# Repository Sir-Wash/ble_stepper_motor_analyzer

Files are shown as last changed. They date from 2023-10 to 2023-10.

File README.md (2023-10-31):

# BLE STEPPER MOTOR ANALYZER

> **_NOTE:_** As for June 24th 2023, added under the spec table a discussion regarding the **max stepper voltage** that can be used.

------
<p align="center">
  <br>
  The analyzer device of the reference design here<br>
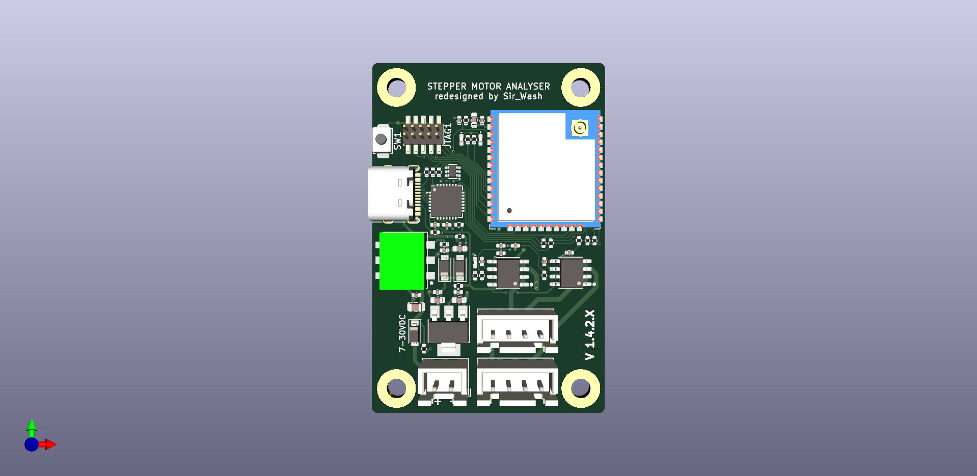
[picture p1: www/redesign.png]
  
</p>

My redsigned design can be found in "\ble_stepper_motor_analyzer\kicad\JLCPCB\Sir_Wash_Redesign"

<p align="center">
  The analyzer's app<br>
  
</p>

**A short video** of the app is available here https://vimeo.com/798169140

---
- [BLE STEPPER MOTOR ANALYZER](#ble-stepper-motor-analyzer)
  - [Description](#description)
  - [Design Highlights](#design-highlights)
  - [How does it work?](#how-does-it-work)
  - [Specification](#specification)
  - [Installing the device in your 3D printer](#installing-the-device-in-your-3d-printer)
  - [Using the Analyzer app.](#using-the-analyzer-app)
    - [Running the Analyzer app using a provided binary](#running-the-analyzer-app-using-a-provided-binary)
    - [Running the Analyzer app using the Python source files](#running-the-analyzer-app-using-the-python-source-files)
    - [Understanding the Analyzer app screen](#understanding-the-analyzer-app-screen)
    - [The Analyzer app buttons](#the-analyzer-app-buttons)
    - [Analyzer app command line flags](#analyzer-app-command-line-flags)
  - [Updating the firmware](#updating-the-firmware)
  - [Building your own device](#building-your-own-device)
  - [Antenna selection](#antenna-selection)
  - [Connectors](#connectors)
  - [3D Models](#3d-models)
  - [Troubleshooting connection issues](#troubleshooting-connection-issues)
  - [Hardware design files](#hardware-design-files)
  - [Firmware development](#firmware-development)
  - [Analyzer App Python development](#analyzer-app-python-development)
  - [FAQ](#faq)

---

## Description

The BLE Stepper Motor Analyzer ('the analyzer') is a low-cost, open source system that analyzes stepper motor signals and display the the data in real time on a computer screen. The system includes two parts:

1. **The Stepper Motor Probe** ('the device'). This is a small electronic board that monitors the currents through the stepper motor wires, extracts information such as steps, and speed, and transmits the data via Bluetooth BLE.

2. **The Analyzer App** ('the app'). This is a Python program that runs on a Windows, MaC OSX, or Linux PC, and displays the stepper information in real time in a graphical view.

The following block diagram shows how the device and the app related to the controller and stepper motor of an existing system such as a 3D printer. 

<p align="center">
 System Block diagram<br>
  
</p>

## Design Highlights
* The device is passive and does not interfere with the operation of the stepper motor, regardless if it is in use or turned off. Furthermore, the stepper signals are galvanically isolated from the electronics.
* Embedding the device in a 3D printer is simple. It has a small footprint, operates on 7-30 VDC, and can use a small external sticker antenna that overcomes shielding by the printer enclosure.
* The design is in the public domain (Creative Commons CC0) and can be used also commercially. Attribution and code sharing are not required.
* The device design is low cost and can be ordered fully assembled from JLCPCB or similar services.
* The device firmware can upgraded by users using a standard USB cable, no tools or adapter required.
* Each device has its fixed unique address such that multiple devices can be used and addressed independently (e.g. one for each stepper motor in your printer).
* Open BLE and Python APIs supports custom monitoring apps, such as specialized analyzers or mobile apps.

## How does it work?
The device contains two galvanic isolated current sensors that sense the currents through the two stepper coils. These values are measured 40,000 times a second and firmware on the device analyzes them and extracts information such as step count, speed, and current patterns. A Bluetooth BLE radio then transmits the data to the app which displays it in a graphical form.

 <p align="center">
 Device Block diagram<br>
  
</p>

## Specification

| Item | Specification |
| :--- | :--- |
| Supply voltage | 7-30 VDC |
| Stepper motor voltage | See note below |
| Power consumption | 1W max |
| Firmware update connector | USB Type C. |
| SOIC Module | ESP32-WROOM-32U-N4. |
| Current measurement | +/-2.5A per coil. |
| PCB | 39mm x 43mm, two layers. |
| Antenna | 2.4Ghz external antenna IPX IPEX connector. |
| Simultaneous connections | 1 max. |
| Protocol | BLE 4.1 or higher, with Data Length Extension feature. |
| Current sensors | CC6920BSO-5A |
| Zero calibration | Using onboard button. |
| Count direction | User selected (doesn't change motor direction). |
| Sampling rate | 40Khz per channel. |
| Sampling resolution | 12bits. |
| Current accuracy | estimated at +/- 2%. |
| Max step rate | 5K full steps/sec. |
| Step resolution | 1/100th of a full step. |
| Firmware programming language | C++ |
| Firmware programming IDE | VSCode, Platformio, ESPIDF framework. |
| Firmware debugging | Via optional 10 pins JTAG connector. |
| Electronic design tool | Kicad. |
| Mechanical design tool | Onshape. |
| Open source license | Creative Commons CC0. |

> **_NOTE:_**  The analyzer uses current sensors CC6920BSO-5A current
sensors which provides galvanic isolation between the stepper motor wires and the circuitry and input voltage of the analyzer. As a result, the stepper motor voltage is not limited, and is independent, of the supply voltage. While the sensors are specified as 3500V RMS isolation, the PCB was definitely not designed for that voltage in mind and use only 6mil clearance between the traces. Some information on the internet such as https://www.smpspowersupply.com/ipc2221pcbclearance.html suggests that this qualifies it to 50 or even 100v, but since we are not safety experts, we tested it with only 24V steppers.

## Installing the device in your 3D printer

1. Print a device carrier using a 3D printer (STL model included here) and attach the device to the carrier using two pieces of 3M VHB 1mm sticky tape or similar.
2. Attach the device carrier to the 3D printer using an additional piece of 3M VHB tape.
3. Connect the external antenna and attach the antenna to the outside of the printer.
4. Connect the motor driver and stepper motor to the two connectors as shown in the wiring diagram below. The two connectors form a path through path, such that one pair of adjacent pins are used for one coil and the other pair for the second coil.
5. Connect 7-30VDC power to the VIN connector of the device. Pay attention to polarity, though the device will not get damaged by reverse polarity. 
6. Do not connect anything to the USB connector. This connector is intended for firmware flashing only.
7. The device installation is complete. You can use your 3D printer just as you did before, regardless if the analyzer app is active or not. To monitor the stepper while your printer is turned on, use the provided analyzer app on your Windows, Mac, or Linux PC as described below. 

&nbsp;

<p align="center">
  Wiring Diagram<br>
  
</p>

## Using the Analyzer app.

### Running the Analyzer app using a provided binary
The simplest way to run the analyzer app on your computer is to look for an  executable file for your system under the 'release' directory in this repository. They also released as 'release.zip' file.

> **_NOTE:_**  The single binary files are created from the app's Python code using the Pyinstaller tool and the scripts in the python/pyinstaller directory.

### Running the Analyzer app using the Python source files
If a single app binary is not available for your system, or if you prefer to run the Python code directly, you will first need to do a few preparation to satisfy the prerequisites of the Python code.

1. Install Python on your computer. Prefer the latest stable version.
2. Clone the repository on your computer or download and extract the 'python.zip' release file.
3. Install the required python modules by running this command the 'python' directory :
   
```
pip install -r requirements.txt
```
4. Make sure that your analyzer device is powered on and start the app using the command

```
python analyzer.py
```

> **_NOTE:_**  When the device is idle, its LED blink at a rate of about 1 blink per second. When connected to the app, it blink faster about 3 blinks per second. The app can connect to a device only when it's idle as indicated by the slower blink rate.

### Understanding the Analyzer app screen

<p align="center">
  
</p>

The apps screen contains the following graphs

* [A]. A rolling chart with distance in steps. Updated 50 times a second.
* [B]. A rolling chart with speed in steps/sec. Updated 50 times a second.
* [C]. A rolling chart with stepper absolute current in Amps. Updated 50 times a second. The absolute current of a stepper is sqrt(A^2 + B^2) where A and B are the momentary currents of coils A, B respectively.
* [D] A histogram of current vs speed that shows how well the driver is able to maintain the stepper current at various speeds. High coil inductance of low power voltage result in significant current level at higher speeds.
* [E] A histogram that shows the relative time spent in each speed range.
* [F] A histogram that shows the relative distance done in each speed range.
* [G] A phase (Lissajous curve) graph that shows the 'cleanliness' of the sine/cosine current signals the driver sends to the motor.
* [H] An oscilloscope graph that shows current samples from the two coils. During stepper movement in a constant speed, they should look like sine/cosine waves. 

> **_NOTE:_**  In the oscilloscope graph, a single sine or cosine cycle represents 4 stepper full steps, as shown in the graph below.

<p align="center">
  
</p>

### The Analyzer app buttons
The Analyzer app contain the button listed below. 

> **_NOTE:_**  The buttons affect the app only and do not interfere with the operation of the motor.

* **Toggle Dir** - Click to change the direction of step counting.
* **Reset Data** - Click to clear the histograms and step count.
* **Time Scale X** - Click to toggle the sampling time of the signals shown in the phase graph [G] and oscilloscope graph [H] to match the movement speed. As a rule of thumb, you want to have at least one full sine/cosine wave, with higher values for slower stepper movements.
* **Pause** - Click to pause/resume the display. Useful examine interesting captured data.

> **_NOTE:_** The graphs are implemented using pyqtgraph and thus provide additional functionality that is accessible by a right mouse click on the graphs.

### Analyzer app command line flags

**--help** Prints a list with the available flags.

**--scan** The analyzer will scan for BLE devices for a few seconds, print a list of  devices it found and exit. This intended for diagnostics. The stepper motor analyzer devices have names that look like <si>STP-0C8B95F2B436</i>.

```
python analyzer.py --scan
```

**--device** Instructs the analyzer to not search on start for available devices, and instead, connect to the device with given name directly. If you set in the device a nick name using the --set-nickname flag below, you can also use that nickname as a value of the --device falg. 

```
python analyzer.py --device "STP-0C8B95F2B436"

python analyzer.py --device "X-AXIS"
```

**--set_nickname** Running the analyzer with this flags sets on the device a user friendly nickname that can be used as an alternative value for the *--device* flag. That nickname is also shown in the title of the Analyzer graphical view.

```
python analyzer.py --set_nickname "X-Axis"
```

**--max-amps** If you monitor a low current stepper motor such as a 600ma extruder motor, you can use this flag to limit the range of the current display in the Phase and Oscilloscope graphs, to zoom in on details.
```
python analyzer.py --max-amps 0.8
```

***--units*** The default units for stepper distance or rotation are full steps. You can use this flag to display other units such as mm, degrees, or extrusion mm^3. 
```
python analyzer.py --units "mm"

python analyzer.py --units "degrees"

python analyzer.py --units "mm^3"
```

**--steps_per_unit** If you are using the **--units** flag, use this flag to specify the number of full motor steps that correspond to one unit. For example, if your extruder esteps value is 540 micro steps per mm, with 16 microsteps per full step, specify the flags below:
```
python analyzer.py --units=mm --steps_per_unit 33.75
```

## Updating the firmware

To flash a firmware version follow these steps.

1. Download the release.zip file of the desired release and extract it.
2. Disconnect the power connector of the device and connect it to your computer using a USB cable.
3. Run the flash script for your Windows, Mac or Linux computer. For example:
```
flash.bat
```
 4. Verify that the the script completed with no errors and that the LED on the device is blinking at about one blink per second. The device with the new firmware is ready.

## Building your own device

1. Order assembled boards (recommended), or just order bare PCBs and assemble the components yourself. Production files for JLCPCB PCB, including for the SMT service are included in this repository.
2. Connect the device to a computer via a USB cable and notice that one LED turn on solid to indicate 3.3V power.
3. Flash the device with firmware as explained above.
4. Calibrate the current sensors for zero level by long pressing the switch until the second LED will blink 3 times to indicate that the calibration values were saved in the non volatile memory.
5. Connect an antenna, run an analyzer program as explain above and that you see some signals from the device. The LED on the device will blink faster to indicate an active connection.
6. The device is now ready for installation in the 3D printer or for shipping to your customers.

* **Schematic**: https://github.com/zapta/ble_stepper_motor_analyzer/blob/main/kicad/stepper_monitor.pdf
* **JLCPCB production files**: https://github.com/zapta/ble_stepper_motor_analyzer/tree/main/kicad/JLCPCB

> **_NOTE:_**  Resistor R16 acts as a jumper and allows to disconnect the 3.3V supply from the rest of the electronics. This is useful when diagnosing power issues.

## Antenna selection

The external antenna should  satisfy these requirements:
* Specified for the Bluetooth band of 2.4GHZ.
* Having a connector that match the ESP32 WROOM module. The connector has several names including IPEX, U.FL, or MHF1, but it's easier to distinguish it by its wider body.

<p align="center">
  
</p>

<p align="center">
  Inexpensive Aliexpress sticker antennas.<br>
  
</p>

## Connectors

* **Stepper Motor Connectors** - KF2510 connector 2.54mm pitch, female, 4 wires.
* **Vin connector** - Dupont 2.54mm pitch, female, 2 wires. 

## 3D Models

3D Models of the carrier and a cover for shipping are available at https://github.com/zapta/ble_stepper_motor_analyzer/tree/main/3D

<p align="center">
  
</p>

## Troubleshooting connection issues

The analyzer requires on the PC side support for Bluetooth BLE 4.1 or higher with support for the Data Length Extension feature. It is expected that most computer come with a built in adapters that support
this standard, but we also observed a very low cost BeeLink mini computer that came with an old internal Bluetooth adapter that doesn't support this standard.

The workaround in this case is to **disable the internal Bluetooth adapter** and use an **external USB Bluetooth adapter** that has an external antenna for better range. For example we had good result with this adapter that as of 2023 cost about $15 https://www.amazon.com/gp/product/B09KGVFX1K, which is based on the RTL876B chip.

<p align="center">
  
</p>

> **_NOTE:_**  Installing a RTL876B based adapter on Ubuntu requires a minor tweak of the firmware file names as explained at https://fosspost.org/fix-bluetooth-rtl8761b-problem-on-linux-ubuntu-22-04/. Also, 

The symptoms of a PC bluetooth adapter that doesn't support the required protocol are that the device shows up when running *analyzer --scan* but when running the analyzer without the *--scan* flag, it fails to connect to the device.  For the more technical readers, a discussion on this topic is available here https://github.com/hbldh/bleak/issues/1227#issuecomment-1435708347

## Hardware design files

The Kicad source files and the generated JLCPCB production files are available under the *kicad* directory of this repository. As of Mar 2023, we are using Kicad 7.0, and the built in plugins **Fabrication Toolkit** and **Interactive Html Bom**.

## Firmware development

This list below outlines the steps to set up your own firmware development environment.

1. Install Visual Studio Code (VSC).
2. In Visual Studio Code, enable the <i>platformio</i> extension.
3. Download or clone this git repository on your computer.
4. In VSC, select <i>File | Open Folder</i> and select the 'platformio' directory.
5. Connect a device to your computer using a USB cable. This will create a serial port on your computer.
6. Click on the platformio <i>Upload</i> icon at the bottom of the screen (right arrow icon) and platformio will automatically install all the dependencies, build the project, and upload it to your device via the serial port.  
7. For more information on how to use platformio, check http://platformio.org.

> **_NOTE:_**  For optional hardware debugging (breakpoints, single step, etc), you will need an Espressif ESP-Prog Development Board, and to solder on your device a 10 pins JTAG connector.

> **_NOTE:_** It's OK to connect a stepper motor to the device while you develope code since the stepper signals are galvanically isolated from the USB interface and from your computer.

> **_NOTE:_** It is recommended to not connect VIN and the USB connectors at the same time to avoid ground loop, in case both the Vin power supply and your computer are grounded independently.

## Analyzer App Python development

The Analyzer's Python app is stored in the 'python/analyzer' directory and uses a library at python/common. The app is based on Bleak (BLE client) PyQtGraph (a graphing library) and uses asyncio for non blocking background operation. The list of requires python modules is in requirements.txt and they can be installed using the command

```
pip install -r requirements.txt
```

## FAQ

**Q**: This is an exciting project, can I help?

A: Of course, contribution of code, documentation, test programs or ideas are welcome.

---

**Q**: I want to monitor multiple motors in my 3D printer. Is it possible?

**A**: Of course. Simply install a device for each stepper motor you want to monitor. 

---

**Q**: I am using multiple devices, how can I select which one I connect to? 

**A**: Each device has a fixed unique name such STP-0C8B95F2B436. When you run the analyzer app, it will allow you to select a device, if more than one are available, or you can use the --device flag to force a specific device.

---

**Q**: How far can my computer be away from my 3D printer? 

**A**: Bluetooth BLE radio communication is intended for short distances of a few yards. If the radio link will not be reliable, the analyzer program will detect data gaps and will report it in its console log.

---

**Q**: This system can be a great idea for a Crowd Compute campaign. Can I do that? 

**A**: Of course. The design is in public domain and commercial usages are encouraged. Attribution and sharing of modification you make are not required. 

---

**Q**: Do you sell boards? 

**A**: We may produce a limited numbers of boards from time to time, but we also believe that others can do a better job job of mass producing and making it available to the community.

---

**Q**: Can the external antenna be eliminated to simplify installation and reduce cost? 

**A**: Yes. We believe that the ESP module ESP32-WROOM-32D-N4 which uses an internal antenna should be a drop-in replacement though we did not have the chance yet to test it.

---

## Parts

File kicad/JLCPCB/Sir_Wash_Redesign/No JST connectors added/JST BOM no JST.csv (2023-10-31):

Designator | Footprint | Quantity | Value | LCSC Part #
C1 | 0805 | 1 | 10u 50V | C440198
C10, C12, C5, C6 | 0603 | 4 | 10u | C96446
C11, C13, C14, C17, C3, C4, C7, C8 | 0402 | 8 | 100n | C307331
C15, C18, R17, R18 | 0402 | 4 | DNP | DNP
C16, C19 | 0402 | 2 | 2n2 | C1531
C2 | 0402 | 1 | 100n 50V | C307331
C9 | 0402 | 1 | 2u2 | C12530
D1, D4 | 0402 | 2 | RED | C71911
D2 | 0402 | 1 | GREEN | C130722
D3 | D2_SOD-123 | 1 | SM4007PL | C64898
D5, D6 | D_SOD-123 | 2 | B5819W | C8598
J4 | USB_C_Receptacle_XKB_U262-16XN-4BVC11 | 1 | USB_C_Receptacle_USB2.0 | C319148
J5 | PinHeader_2x05_P1.27mm_Vertical_SMD | 1 | JTAG | DNP
Q1 | SOT-363_SC-70-6 | 1 | MMDT2222A | C96379
R1, R10, R11, R2, R4, R5, R6, R7 | 0402 | 8 | 5K1 | C25905
R12, R13, R8, R9 | 0402 | 4 | 10K | C25744
R14, R15, R19, R20 | 0402 | 4 | 1K | C11702
R16 | 0402 | 1 | 0R | C17168
R3 | 0402 | 1 | 200K | C25764
SW1 | SW_Push_SPST_NO_Alps_SKRK | 1 | SW_Push | C720477
U1 | Converter_DCDC | 1 | 5V | C2684892
U2 | QFN-28-1EP_5x5mm_P0.5mm_EP3.35x3.35mm | 1 | CP2102-GMR-QFN28 | C6568
U3 | SOT-223-3_TabPin2 | 1 | AMS1117-3.3 | C6186
U4, U5 | SOIC-8_3.9x4.9mm_P1.27mm | 2 | CC6920BSO-5A | C2880430
U6 | ESP32-WROOM-32U | 1 | ESP32-WROOM-32U-N4 | C328062

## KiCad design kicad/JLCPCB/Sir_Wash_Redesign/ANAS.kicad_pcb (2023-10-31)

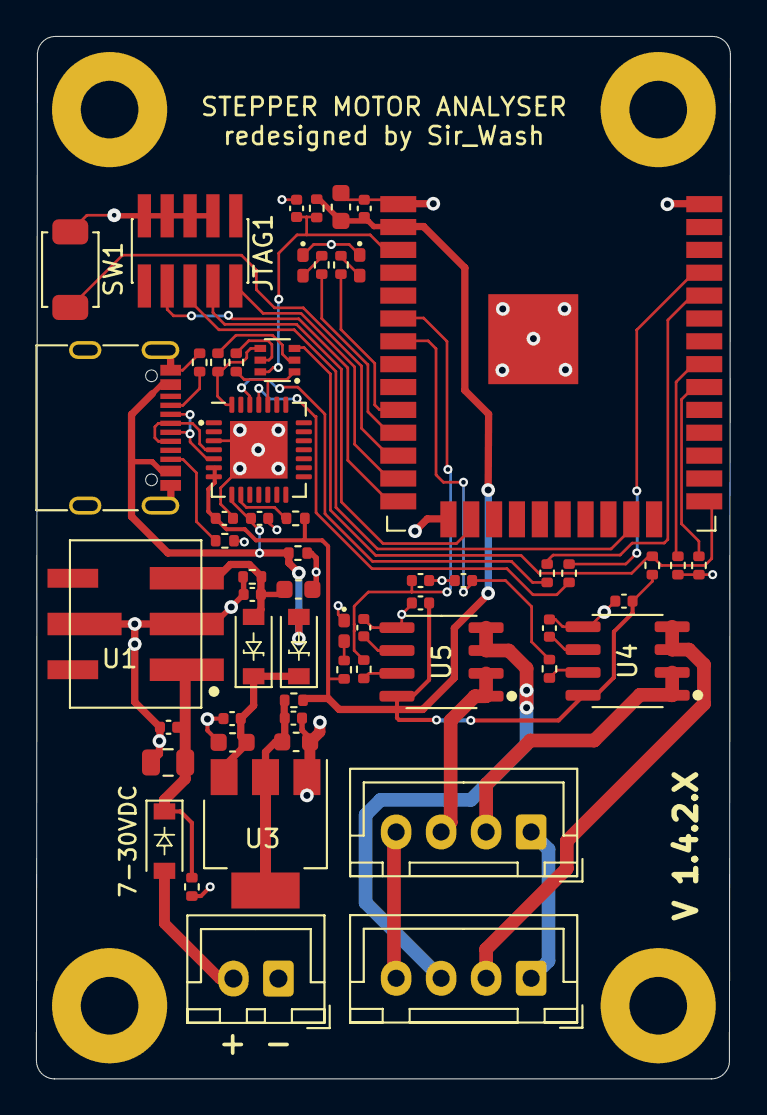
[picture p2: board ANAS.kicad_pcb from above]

Board: 2 copper layers, 38.6 x 57.9 mm, 62 parts (0 on the bottom side), 47 nets.

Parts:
C1: 10u 50V; C_0805_2012Metric
C2: 100n 50V; C_0402_1005Metric
C3, C4, C7, C8, C11, C13, C14, C17: 100n; C_0402_1005Metric
C5, C6, C10, C12: 10u; C_0603_1608Metric
C9: 2u2; C_0402_1005Metric
C15, C18: DNP; C_0402_1005Metric
C16, C19: 2n2; C_0402_1005Metric
D1, D4: RED; LED_0402_1005Metric_Pad0.77x0.64mm_HandSolder
D2: GREEN; LED_0402_1005Metric_Pad0.77x0.64mm_HandSolder
D3: SM4007PL; D2_SOD-123
D5, D6: B5819W; D_SOD-123
H1, H2, H3, H4: MountingHole_Pad; MountingHole_3.2mm_M3_Pad
J1, J2: JST-XH_01x04_Pin; JST_XH_B4B-XH-A_1x04_P2.50mm_Vertical
J3: JST-XH_01x02_Pin; JST_XH_B2B-XH-A_1x02_P2.50mm_Vertical
J4: USB_C_Receptacle_USB2.0; USB_C_Receptacle_XKB_U262-16XN-4BVC11
J5: JTAG; PinHeader_2x05_P1.27mm_Vertical_SMD
Q1: MMDT2222A; SOT-363_SC-70-6
R1, R2, R4, R5, R6, R7, R10, R11: 5K1; R_0402_1005Metric
R3: 200K; R_0402_1005Metric
R8, R9, R12, R13: 10K; R_0402_1005Metric
R14, R15, R19, R20: 1K; R_0402_1005Metric
R16: 0R; R_0402_1005Metric
R17, R18: DNP; R_0402_1005Metric
SW1: SW_Push; SW_Push_SPST_NO_Alps_SKRK
U1: 5V; Converter_DCDC
U2: CP2102-GMR-QFN28; QFN-28-1EP_5x5mm_P0.5mm_EP3.35x3.35mm
U3: AMS1117-3.3; SOT-223-3_TabPin2
U4, U5: CC6920BSO-5A; SOIC-8_3.9x4.9mm_P1.27mm
U6: ESP32-WROOM-32U-N4; ESP32-WROOM-32U

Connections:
+3V3: C7.1, C12.2, C13.1, C14.2, C17.2, R6.2, R7.2, R12.2, R13.2, R16.1, U2.6 (VDD), U2.7 (REGIN), U4.8 (VCC), U5.8 (VCC), U6.2 (VDD)
CFG1: R17.1, U6.30 (IO18)
CFG2: R18.1, U6.31 (IO19)
CHA: C19.1, R20.1, U6.6 (IO34)
CHB: C16.1, R19.1, U6.7 (IO35)
D+: J4.A6 (D+), J4.B6 (D+), U2.4 (D+)
D-: J4.A7 (D-), J4.B7 (D-), U2.5 (D-)
DTR: Q1.4 (E2), R10.1, U2.28 (~DTR)
EN: C9.2, Q1.6 (C1), R12.1, U6.3 (EN)
ESP_TCK: J5.4, U6.16 (IO13)
ESP_TDI: J5.8, U6.14 (IO12)
ESP_TDO: J5.6, U6.23 (IO15)
ESP_TMS: J5.2, U6.13 (IO14)
GNDD: C1.1, C2.1, C3.1, C4.1, C5.1, C6.1, C7.2, C8.1, C9.1, C10.1, C11.1, C12.1, C13.2, C14.1, C15.1, C16.2, C17.1, C18.1, C19.2, D1.1 (K), D2.1 (K), D4.1 (K), J3.1, J4.G (GND), J4.SHLD, J5.3, J5.5, J5.7, J5.9, R3.2, R4.1, R5.1, R8.1, R9.1, R17.2, R18.2, SW1.1, U1.2 (GND), U1.5 (GND), U2.3 (GND), U2.29 (GND), U3.1 (GND), U4.5 (GND), U5.5 (GND), U6.1 (GND), U6.15 (GND), U6.38 (GND), U6.39 (GND)
IO0: Q1.3 (C2), R13.1, U6.25 (IO0)
LED1: R1.2, U6.11 (IO26)
LED2: R2.2, U6.10 (IO25)
unnamed: D1.2 (A), R1.1
unnamed: D2.2 (A), R2.1
unnamed: D3.2 (A), J3.2
unnamed: C1.2, C2.2, D3.1 (K), R3.1, U1.1 (IN)
unnamed: D4.2 (A), R6.1
unnamed: C6.2, C8.2, D5.1 (K), D6.1 (K), U3.3 (VI)
unnamed: C3.2, C5.2, D6.2 (A), R8.2, U1.3 (OUT)
unnamed: J1.1, J2.1
unnamed: J1.2, U4.1 (+), U4.2 (+)
unnamed: J1.3, U5.1 (+), U5.2 (+)
unnamed: J1.4, J2.4
unnamed: J2.2, U4.3 (-), U4.4 (-)
unnamed: J2.3, U5.3 (-), U5.4 (-)
unnamed: J4.A5 (CC1), R4.2
unnamed: J4.B5 (CC2), R5.2
unnamed: Q1.2 (B1), R10.2
unnamed: Q1.5 (B2), R11.1
unnamed: R14.2, U2.25 (RXD)
unnamed: R15.2, U2.26 (TXD)
unnamed: R7.1, U2.9 (~RSTb)
unnamed: C10.2, C11.2, R16.2, U3.2 (VO)
unnamed: C15.2, U4.6 (NC)
unnamed: R19.2, U4.7 (VIOUT)
unnamed: C18.2, U5.6 (NC)
unnamed: R20.2, U5.7 (VIOUT)
RTS: Q1.1 (E1), R11.2, U2.24 (~RTS)
RXD0: R15.1, U6.34 (RXD0/IO3)
SWITCH: SW1.2, U6.12 (IO27)
TXD0: R14.1, U6.35 (TXD0/IO1)
VBUS: C4.2, D5.2 (A), J4.VB (VBUS), R9.2, U2.8 (VBUS)
